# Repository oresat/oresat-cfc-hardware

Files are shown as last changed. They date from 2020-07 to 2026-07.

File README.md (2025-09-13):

# oresat-cfc-hardware

Cirrrus Flux Camera hardware repository. See also https://www.oresat.org/satellites/oresat/mission-2-cfc.

## General information
The Cirrus Flux Camera (CFC) is a Short Wave Infrared (SWIR) camera meant to map the global distribution of high-altitude cirrus clouds. It works by looking at the reflected sunlight from clouds in three SWIR bands. The primary investigators (PIs) for CFC calibration, data processing, and climate science are our collaborators at the [University of Maryland Baltimore Count (UMBC)'s Earth and Space Institute (ESI)](https://esi.umbc.edu/) as well as by our collaborators at the [University College London (UCL) Mullard Space Science Laboratory (MSSL)](https://www.ucl.ac.uk/mathematical-physical-sciences/mssl).

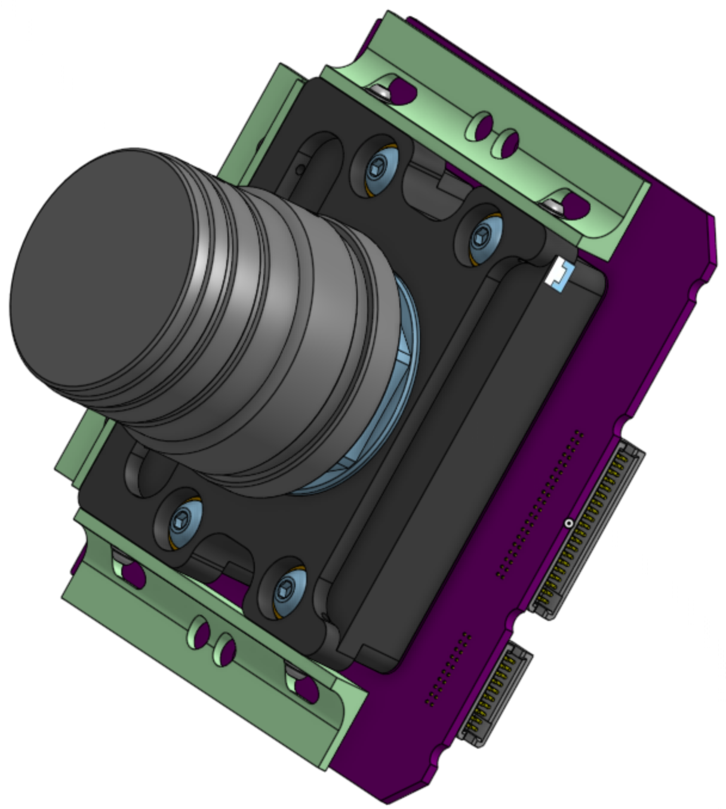
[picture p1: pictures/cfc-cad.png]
CFC Assembly CAD model


Older versions of the CFC flew on the [2022 NASA High Altitude Student Payload (HASP)](https://sg-webserver.phys.lsu.edu/) mission.

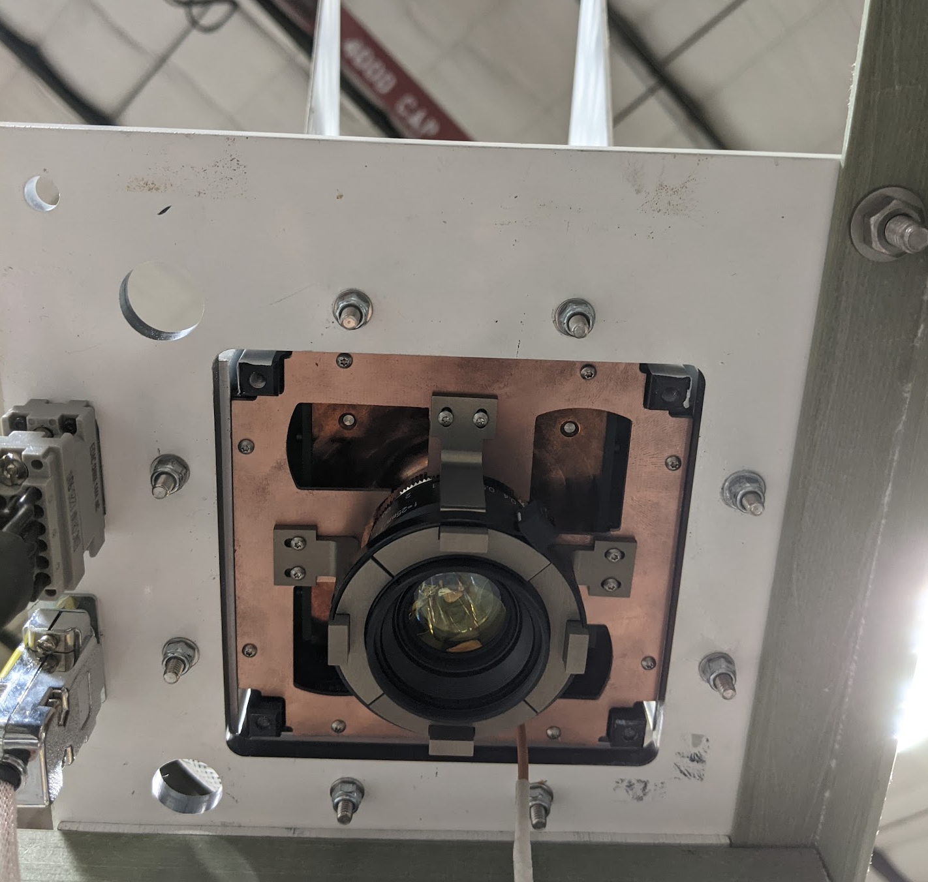
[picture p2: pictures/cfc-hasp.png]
CFC on HASP balloon


Different but modern versions were flown by [UMBC's AirHARP mission](https://esi.umbc.edu/airharp2-at-pace-pax/) on the NASA ER-2 high altitude plane.

Most recently, we flew a preliminary technology demonstration mission on [OreSat0.5](https://www.oresat.org/satellites/oresat0-5) launched August 16th, 2024.

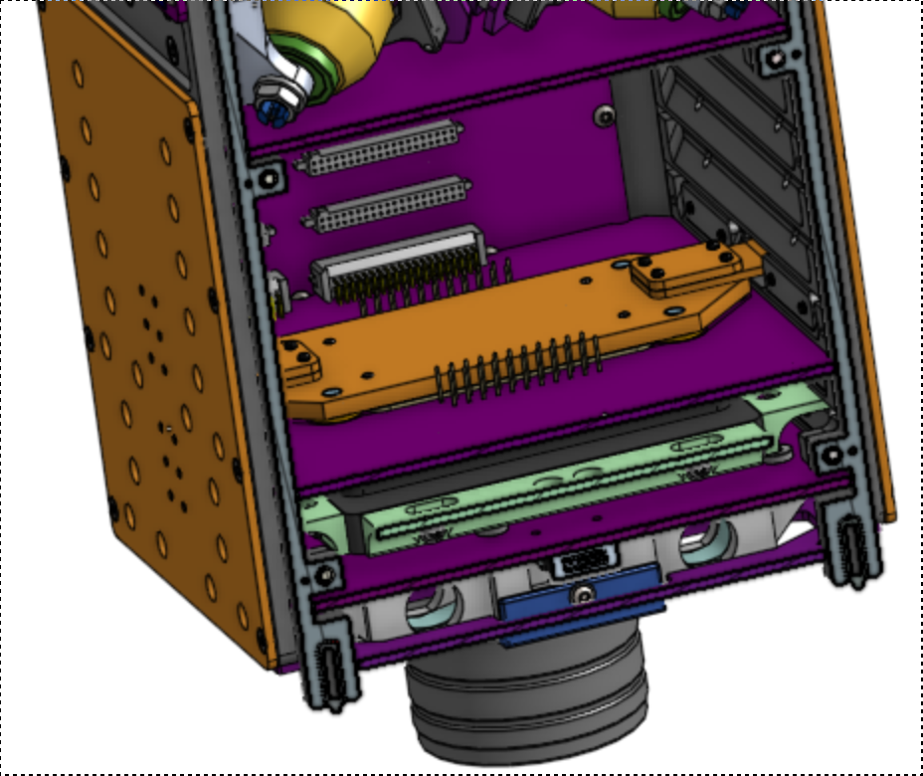
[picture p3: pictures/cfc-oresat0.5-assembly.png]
CFC on OreSat0.5


We're planning on flying the science mission camera on OreSat1 in Q2 2026.

Versions of the CFC have also flown on the NASA High Altitude Student Payload (HASP) in New Mexico, and 
## Technical information about the CFC sensor

- Princeton IR PIRT1280 InGaAs focal plane array (1280 x 1024 with 12 um pixels), sensitive to roughly 800 - 1600 nm.
- We cool the sensor to -8 deg C using its built-in thermal electric cooler (TEC - just a standard Peltier device).
- We use three filters on the PIRT1280 sensors:
   - 870 nm: [Torrent Photonics Optical Filter Shop 2020OFS-870](https://opticalfiltershop.com/shop/bandpass-filter/nir-bandpass-700nm-to-1100nm/nir-bandpass-filter-870nm-fwhm-30nm/)
   - 1390 nm: [Torrent Photonics Optical Filter Shop 2020OFS-1390](https://opticalfiltershop.com/shop/bandpass-filter/swir-bandpass-filters-1-1um-to-3-0um/swir-bandpass-filter-1390nm-fwhm-35nm/)
   - 1590 nm: [Torrent Photonics Optical Filter Shop 2020OFS-1590](https://opticalfiltershop.com/shop/bandpass-filter/swir-bandpass-filters-1-1um-to-3-0um/swir-bandpass-filter-1590nm-fwhm-40nm/)
- Lens is the [Navitar SWIR-35](https://store.navitar.com/swir-35-35-mm/), a 35 mm  SWIR lens with focus adjustable apateur. 

## Technical information on the system

- The **CFC Sensor Card** is a PCB in backplane slot 18. It has:
   - The PIRT 1280 sensor soldered on the PCB
   - A custom machined lens adapter between the card and the lens.
   - Custom machined G10 L brackets between the custom machined lens adapter and slot 19 
   - The lens on the adapter sticks through the -Z end card, through the -Z end cap, and finally out into the tuna can volume. A 3D printed adapter on the End Card holds the monopole deployers and holds the camera lens at the End Card and End Cap levels.
   - The SWIR lens sticks into the tuna-can space on the -Z end of OreSat0.5 and OreSat1.
- The **CFC Processor Card** is a PCB in backplane slot 17 with:
   - LVDS to PRU adapter IC
   - an [Octavo OSD335x-SM](https://octavosystems.com/octavo_products/osd335x-sm/) system in package (SIP) processor with 1 GB DRAM and a 16 GB eMMC storage IC.
 - Radiator
    - The top of the CFC Sensor Card has a large block of copper being used as a heat spreader. The heat spreader dumps the heat from the TEC into thin copper leaf springs that lead the heat to two external copper radiators in the -Z+Y and -Z-Y solar module positions. These copper radiators are covered by a high emissivity tape.
    
## Design Notes

- Mostly on our Google Drive right now, here's the beginnings of our [CFC Design Notes](https://docs.google.com/document/d/1nDrTuUim9k1om3DOcBtnp3ixVvrmmALAsb2CZlDwwio/edit?usp=sharing).

## Links to CAD

- [OreSat CFC Camera mechnical in OnShape](https://cad.onshape.com/documents/0e986a82427039a7549eafca/v/f54f3484c685a75ab5bd82ce/e/deddd282159689e0e52f600b)
- [OreSat0.5 containing the CFC assembly in OnShape](https://cad.onshape.com/documents/c0a6cf3367d8fdcad3a3c2e1/w/ca55e3ec6f041493d70e4b39/e/591851cdc8c634aae1522f90)
- [Electronics CAD on Github](https://github.com/oresat/oresat-cfc-hardware) - mostly KiCad with some older EAGLE files.
- [Kernel module](https://github.com/oresat/oresat-prucam-pirt1280) for the PIRT 1280 on the Octavo's PRU.

## License

All materials in this repo are copyright Portland State Aerospace Society and are licensed under the CERN Open Hardware Licence Version 2 -
Strongly Reciprocal (CERN-OHL-S v2), or any later version. A copy of the license is located in [here](LICENSE.md).

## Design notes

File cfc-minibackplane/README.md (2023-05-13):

# Oresat CFC Mini-Backplane

This is the backplane for UMBC's Air Harp 2 sensor, which is going to include a PIRT SWIR sensor using OreSat's CFC system.

## Requirements:

* Match the DXF outline from Joe, including placement of connectors and the fastener holes.
   * Probably remove solder mask from both sides of those fastener holes just in case.
   * Probably put the external connectors in the upper right hand corner.
* Use an OreSat 20 pin debug connector on this backplane so we can run USB from the CFC processor to the external connector using the CFC processor's debug connector.
* External connections
   * Power should come through a 0.2 inch euroterminal for two 20 AWG wires.
   * USB should be via a [Harwin M80-5400442](https://www.digikey.com/en/products/detail/harwin-inc/M80-5400442/4953167) connector. Pin-out is determined by us.
       * signals: USB D+, USB D-, Vbus, and GND.
       * Vbus should go through a 10k ohm resistor between the 20 pin debug connector and the Harwin connector.
       
## Required changes to the CFC Processor and CFC sensor boards

Easiest thing to do:

* Both OPDs should come on by default, so we need to bypass or hack the OPDs to turn on.
* We may want to figure out some way to power the local OPDs so they're not doing anything weird with their connections to the Octavo.

A Ben Idea:

* Add a 8.4V to 5V LDO, a Trinket M0, two 4.7K resistors, and use Oliver Rew's Arduino code to turn on both CFC cards
* This assumes we have Trinkets, which I believe we have a bunch lying around.
* This is cute because we don't have to modify the sensor or processor card, which I hate doing.
* Be careful of the 8.4V max input voltage can power the trinket without frying it (thus the 5V LDO).

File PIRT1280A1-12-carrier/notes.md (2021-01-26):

Did a large search for low noise LDOs, found the LT3042. There are various flavors; get large temperature version, automative, if possible.

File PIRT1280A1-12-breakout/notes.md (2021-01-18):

100 ohm Differential pairs on OSH Park 4 layer 
* Found the trace width here. https://www.reddit.com/r/ECE/comments/2ttd3t/differential_trace_impedance_matching_question/
* Used https://www.everythingrf.com/rf-calculators/differential-microstrip-impedance-calculator
* Used https://www.eeweb.com/tools/edge-coupled-microstrip-impedance/
* Assumptions: t = 1.4 mils, , h = 6.7 mils,  Er = 3.69
* diff microsrtips of w = 15 mils, s = 10 mils --> 100.59 differential

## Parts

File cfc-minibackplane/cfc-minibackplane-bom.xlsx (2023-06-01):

Qty | P/DNP | Parts | MFR | MPN | Description | Generic | Assembly | Stock | Dist | DPN | Notes
2 | P | C1.1, C1.2 | Murata | GCM1885C2A102JA16D | 1000 pF ±5% 100V Ceramic Capacitor C0G, NP0 0603 AEC-Q200 | Y |  |  | Digi-Key | 490-4772-1-ND | CAN termination
2 | NP | C3.1, C3.2 | Murata | GCM1885C2A102JA16D | 1000 pF ±5% 100V Ceramic Capacitor C0G, NP0 0603 AEC-Q200 | Y |  |  | Digi-Key | 490-4772-1-ND | CAN termination
4 | P | C1, C2, C3, C4 | Murata | GCM31CC71E106KA03K | 10 µF ±10% 25V Ceramic Capacitor X7S 1206 AEC-Q200 | Y |  |  | Digi-Key | 490-14533-1-ND | Note working voltage
3 | P | CF1.1, CF2.1, CF3.1 | Samtec | SFM-110-01-L-D-LC | 20 Position Receptacle Connector 0.050" (1.27mm) Through Hole Gold | N |  |  | Digi-Key | SFM-110-01-L-D-LC-ND | Auxiliary connector: Also SFM-110-[01|03|L1|L3]-[L|S|F]-D-LC
3 | P | CF1.2, CF2.2, CF3.2 | Samtec | SFM-120-01-L-D-LC | 40 Position Receptacle Connector 0.050" (1.27mm) Through Hole Gold | N |  |  | Digi-Key | SFM-120-01-L-D-LC-ND | Main connector: Also SFM-120-01-[L|S|F]-D-LC
1 | P | J1 | Harwin | M55-6001642R | 16 Position Receptacle Connector 0.050" (1.27mm) Surface Mount Gold | N |  |  | Digi-Key | 952-3836-1-ND | Backplane debug connector
1 | P | J2 | Harwin | M80-5100442 | Connector Header Through Hole 4 position 0.079" (2.00mm) | N |  |  | Digi-Key | 952-2343-ND | USB Connector
1 | P | J3 | Phoenix Contact | 1809267 | 2 Position Terminal Block Header, Male Pins, Shrouded (4 Side) 0.200" (5.08mm) Vertical Through Hole | N |  |  | Digi-Key | 277-2619-ND | Power connector
1 | P | J4 | TE | 2-1734592-0 | 20 Position FPC Connector Contacts, Bottom 0.020" (0.50mm) Surface Mount, Right Angle | N |  |  | Digi-Key | A100287CT-ND | Card debug connector
2 | P | R4, R5 | Stackpole | RMCF0603ZT0R00 | 0 Ohms Jumper Chip Resistor 0603 AEC-Q200 Thick Film | Y |  |  | Digi-Key | RMCF0603ZT0R00CT-ND | CAN jumpers
4 | P | R1.1, R1.2, R1.3, R1.4 | Rohm | ESR18EZPF60R4 | 60.4 Ohms Â±1% 0.5W, 1/2W Resistor 1206 AEC-Q200 | Y |  |  | Digi-Key | RHM60.4AFCT-ND | CAN termination
4 | NP | R3.1, R3.2, R3.3, R3.4 | Rohm | ESR18EZPF60R4 | 60.4 Ohms Â±1% 0.5W, 1/2W Resistor 1206 AEC-Q200 | Y |  |  | Digi-Key | RHM60.4AFCT-ND | CAN termination
1 | P | R2, R3 | Stackpole | RMCF0603FT4K70 | 4.7 kOhms ±1% 0.1W, 1/10W Chip Resistor 0603 (1608 Metric) Automotive AEC-Q200 Thick Film | Y |  |  | Digi-Key | RMCF0603FT4K70CT-ND | OPD pullups
1 | P | R1 | Stackpole | RMCF0603FT100K | 100 kOhms ±1% 0.1W, 1/10W Chip Resistor 0603 (1608 Metric) Automotive AEC-Q200 Thick Film | Y |  |  | Digi-Key | RMCF0603FT100KCT-ND | Vbus connection
1 | P | U1 | Adafruit Industries | 3500 | ATSAMD21E18 Trinket M0 SAM D ARM® Cortex®-M0+ MCU 32-Bit Embedded Evaluation Board | N |  |  | Digi-Key | 1528-2361-ND | OPD controller
1 | P | U2 | UMW | AMS1117-3.3 | Linear Voltage Regulator IC Positive Fixed 1 Output 1A SOT-223-3L | Y |  |  | Digi-Key | 4518-AMS1117-3.3CT-ND | 3.3V regulator
For debugging / testing
Qty | P/DNP | Parts | MFR | MPN | Description | Generic | Assembly | Stock | Dist | DPN | Notes
3 | NP | N/A | Harwin | M80-4600442 | 4 Position Rectangular Receptacle Connector Crimp Gold 22 AWG | N |  |  | Digi-Key | 952-2625-ND | USB connector
3 | NP | N/A | Phoenix Contact | 1757019 | 2 Position Terminal Block Plug, Female Sockets 0.200" (5.08mm) 180° Free Hanging (In-Line) | N |  |  | Digi-Key | 277-1011-ND | Power connector. Alternative: 1861690

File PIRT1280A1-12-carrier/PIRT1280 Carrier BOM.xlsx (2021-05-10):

Qty | Parts | MFR | MPN | Description | DIS | DPN
6 | C19, C22, C28, C29, C32, C37 | Murata | GCM155R71H102KA37D | CAP CER 1000PF 50V X7R 0402 | Digi-Key | 490-4761-1-ND
6 | C20, C23, C27, C30, C33, C36 | Murata | GCM155R71H103KA55D | CAP CER 10000PF 50V X7R 0402 | Digi-Key | 490-4762-1-ND
5 | C12, C13, C14, C15, C16 | TDK | CGA3E3X5R1E474K080AB | CAP CER 0.47UF 25V X5R 0603 | Digi-Key | 445-12468-1-ND
6 | C21, C24, C26, C31, C34, C35 | Murata | GCM155R71H104KE02J | CAP CER 0.1UF 50V X7R 0402 | Digi-Key | 490-14514-1-ND
3 | C11, C18, C40 | TDK | CGA3E2X8R1E104K080AA | CAP CER 0.1UF 25V X8R 0603 | Digi-Key | 445-5885-1-ND
1 | C17 | TDK | CGA3E1X7R1E105K080AC | CAP CER 1UF 25V X7R 0603 | Digi-Key | 445-6931-1-ND
10 | C1, C2, C3, C4, C5, C6, C7, C8, C9, C10 | TDK | CGA3E1X5R0J475K080AC | CAP CER 4.7UF 6.3V X5R 0603 | Digi-Key | 445-6934-1-ND
1 | C25 | Murata | GRT188R61C106KE13J | CAP CER 10UF 16V X5R 0603 | Digi-Key | 490-GRT188R61C106KE13JTR-ND
2 | D1, D2 | Vishay | TLMG1100-GS08 | LED GREEN 0603 SMD | Digi-Key | 751-1165-1-ND
1 | FB1 | Murata | BLM18KG300JH1D | FERRITE BEAD 30 OHM 0603 1 LN | Digi-Key | 490-14027-1-ND
1 | J12 | TE | 292303-7 | USB-A (USB TYPE-A) USB 2.0 Receptacle Connector 4 Position SMT,RA ; TH | Digi-Key | A115151-ND
1 | J13 | Molex | 395430002 | 2 Position Wire to Board Terminal Block Horizontal 5.00mm TH | Digi-Key | WM12755-ND
1 | J14 | CUI | PJ-202A | Power Barrel Connector Jack 2.10mm ID 5.50mm OD TH RA | Digi-Key | CP-202A-ND
1 | J9 | Wurth | 68715014522 | 50 Position FPC Connector Contacts, Bottom 0.020" (0.50mm) SMT RA | Digi-Key | 732-3522-1-ND
1 | PCB1 | GHI | POCKETBEAGLE-SC-569 | OSD3358 PocketBeagle series ARM® Cortex®-A8 MPU Embedded Evaluation Board | Digi-Key | POCKETBEAGLE-SC-569-ND
1 | Q1 | On Semi | FDD8782 | N-Channel 35A (Tc) 50W (Tc) Surface Mount TO-252AA | Digi-Key | FDD8782TR-ND
5 | R13, R14, R15, R16, R17 | Vishay | MCT0603MZ0000ZP500 | 0 RESISTOR .0603-A | Digi-Key | 749-1745-1-ND
3 | R25, R26, R27 | Stackpole | RMCF0402FT100R | 100 ±1% 0.063W, 1/16W Chip Resistor 0402 AEC-Q200 Thick Film | Digi-Key | RMCF0402FT100RCT-ND
2 | R1, R28 | Panasonic | ERJ-3EKF1001V | 1k RESISTOR .0603-A | Digi-Key | P1.00KHCT-ND
1 | R4 | Panasonic | ERJ-3EKF9091V | 9.09k RESISTOR .0603-A | Digi-Key | P9.09KHCT-ND
1 | R2 | Panasonic | EXB-2HV103JV | 10k RES_EXB2HV | Digi-Key | Y1103CT-ND
1 | R20 | Panasonic | EXB-A10P103J | 10k ARRAY_EXBA-M | Digi-Key | U7103CT-ND
1 | R5 | Panasonic | ERJ-3EKF1622V | 16.2k RESISTOR .0603-A | Digi-Key | P16.2KHCT-ND
1 | R19 | Panasonic | ERJ-6ENF2052V | 20k RESISTOR .0805-A | Digi-Key | P20.5KCCT-ND
1 | R3 | Panasonic | ERJ-3EKF2942V | 29.4k RESISTOR .0603-A | Digi-Key | P29.4KHCT-ND
2 | R6, R7 | Panasonic | ERJ-3EKF33R2V | 33.2k RESISTOR .0603-A | Digi-Key | P33.2HCT-ND
1 | R18 | Panasonic | ERJ-6ENF2053V | 200k RESISTOR .0805-A | Digi-Key | P205KCCT-ND
5 | U1, U2, U3, U4, U5 | Analog Devices | LT3042IMSE#TRPBF | Linear Voltage Regulator IC Positive Adjustable Output 200mA 10-MSOP-EP | Digi-Key | LT3042IMSE#TRPBFCT-ND
1 | U6 | TI | LM2901QPWRQ1 | Comparator Differential CMOS, MOS, Open-Collector, TTL 14-TSSOP | Digi-Key | 296-18438-1-ND
1 | U7 | TI | DS90CR218AMTD/NOPB | 3.3V Rising Edge Data Strobe LVDS 21-Bit Channel Link - 12 Mhz to 85 Mhz | Digi-Key | DS90CR218AMTD/NOPB-ND
1 | X1 | Abracon | ASDAIG-16.000MHZ-X-K-S-T | OSC XO 16.000MHZ 3.3V CMOS SMD | Digi-Key | 535-ASDAIG-16.000MHZ-X-K-S-TCT-ND
ON BREAKOUT BOARD
1 | J1 | Wurth | 68715014522 | 50 Position FPC Connector Contacts, Bottom 0.020" (0.50mm) SMT RA | Digi-Key | 732-3522-1-ND
5 | C100, C101, C102, C103, C104 | AVX | 08055C104K4T4A | 100n ±10% 50V Ceramic Capacitor X7R 0805 | Digi-Key | 478-10546-1-ND

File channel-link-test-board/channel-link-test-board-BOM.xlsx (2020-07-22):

Bill Of Materials for Channel Link Test Board
source file: channel-link-test-board.sch
Last modified: 2020/07/21
PCB version: 1.0 |  |  | P/DNP = | Place/Do Not Place (DNP is for final production boards)
BOM revision: 1 |  |  | Generic = | Any generic part with the same characteristics are OK (e.g., bypass cap)
Cnt | Part References | P/DNP | Mfg | Mfg PN | Description | Generic | Dist | Dist Part Number
1 | JP3 | P | Wurth | 61300311121 | CONN HEADER VERT 3POS 2.54MM | Y | Digi-Key | 732-5316-ND
2 | JP1, JP2 | P | Amphenol | 71918-160LF | CONN HEADER VERT 60POS 2.54MM | Y | Digi-Key | 609-3528-ND
4 | R1, R2, R3, R4 | P | Yageo | RC0201FR-07100RL | RES SMD 100 OHM 1% 1/20W 0201 | Y | Dgi-Key | 311-100MCT-ND
2 | R5, R6 | P | Yageo | RC0603FR-07100RL | RES SMD 100 OHM 1% 1/10W 0603 | Y | Digi-Key | 311-100HRCT-ND
12 | C13, C15, C16, C17, C18, C32, C33, C34, C35, C36, C14, C31 | P | Kemet | C0805C104Z5VACTU | CAP CER 0.1UF 50V Y5V 0805 | Y | Digi-Key | 399-1177-1-ND
1 | R7 | P | Yageo | RC0603FR-0710KL | RES SMD 10K OHM 1% 1/10W 0603 | Y | Digi-Key | 311-10.0KHRCT-ND
12 | C7, C8, C9, C10, C11, C26, C27, C28, C29, C30, C12, C25 | P | Kemet | C0603C103M5RACTU | CAP CER 10000PF 50V X7R 0603 | Y | Digi-Key | 399-7842-1-ND
2 | C37, C38 | P | Murata | GRM188R61A106KE69J | CAP CER 10UF 10V X5R 0603 | Y | Digi-Key | 490-14372-1-ND
12 | C1, C2, C3, C4, C5, C6, C19, C20, C21, C22, C23, C24 | P | Murata | GRM155R71H102KA01J | CAP CER 1000PF 50V X7R 0402 | Y | Digi-Key | 490-6350-1-ND
1 | U1 | P | Texas Instruments | DS90CR218AMTD/NOPB | IC INTERFACE SPECIALIZED 48TSSOP | N | Digi-Key | DS90CR218AMTD/NOPB-ND
1 | U2 | P | Texas Instruments | DS90CR218AMTD/NOPB | IC INTERFACE SPECIALIZED 48TSSOP | N | Digi-Key | DS90CR218AMTD/NOPB-ND

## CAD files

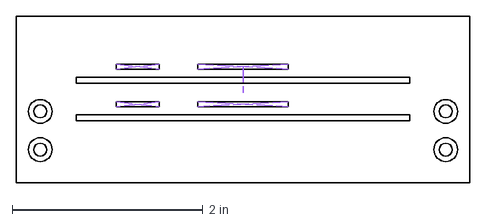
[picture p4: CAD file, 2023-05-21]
cfc-minibackplane/AH2_SWIRminiBackplaneBoard_2023-05-18.dxf
4.75 x 1.75 in

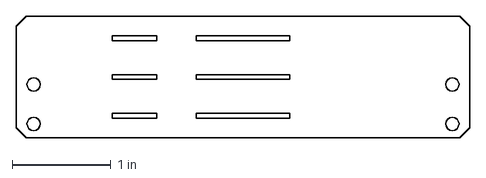
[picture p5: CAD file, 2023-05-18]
cfc-minibackplane/AH2_SWIRminiBackplaneBoard_2023-05-16.dxf
4.60 x 1.23 in

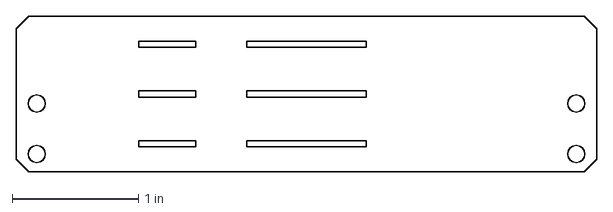
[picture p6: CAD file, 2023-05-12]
cfc-minibackplane/cfc-minibackplane.dxf
4.60 x 1.23 in

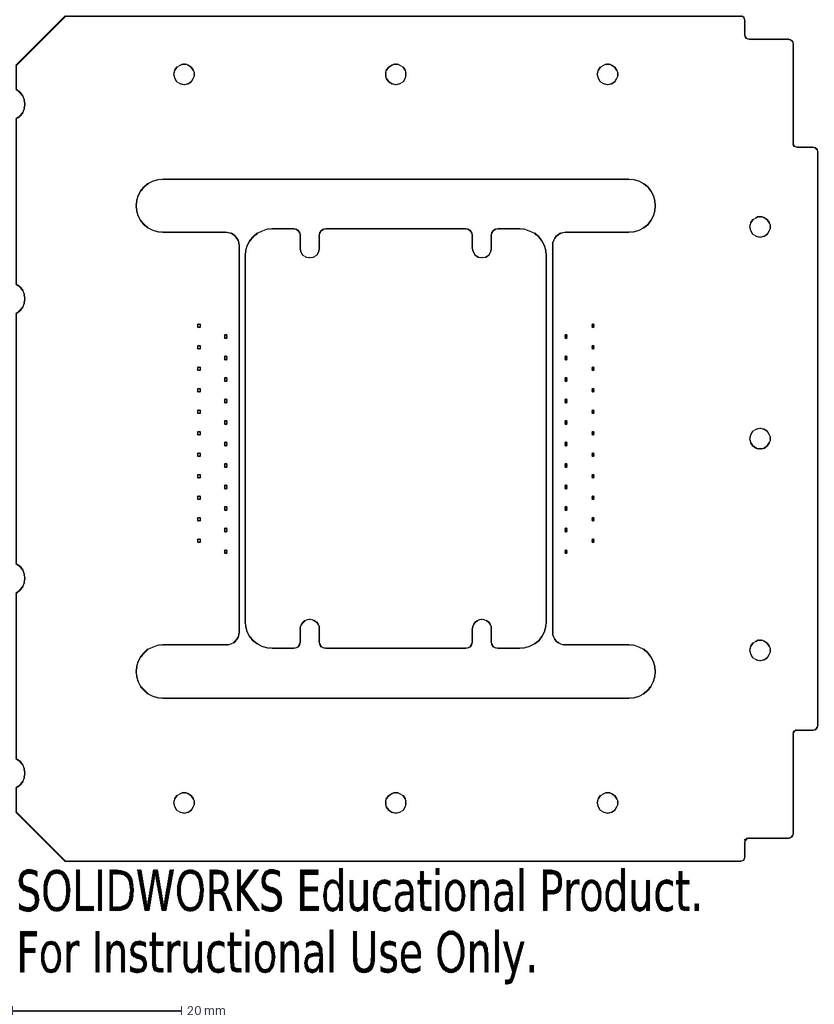
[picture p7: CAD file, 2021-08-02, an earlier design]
cfc-sensor-card-v1/CFCcard.DXF
SOLIDWORKS Educational Product.
For Instructional Use Only.

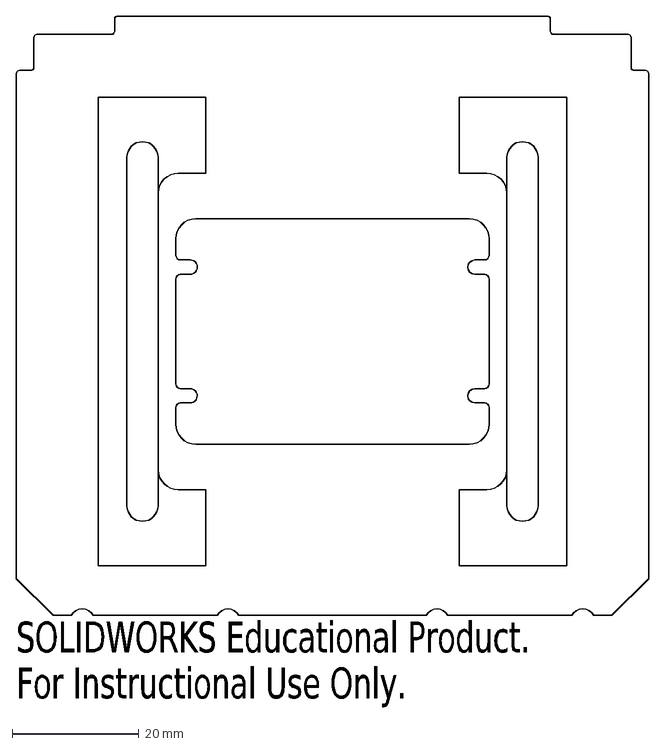
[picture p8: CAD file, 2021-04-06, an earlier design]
cfc-sensor-card-v1/CFCdxf.DXF
SOLIDWORKS Educational Product.
For Instructional Use Only.

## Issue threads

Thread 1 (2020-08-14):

CFC Processor: PLL_VCC and PLL_GND are swapped on the DS90CR217

davidalay, 2020-08-14:
The PLL_VCC and PLL_GND pins need to be swapped on the DS90CR217, currently the board will short with a 30 ohm impedance without a mod.  The footprint on the DS90CR218 is correct

andrewgreenberg, 2025-09-14:
This was fixed as far as I can tell long ago.

Closed 2025-09-14.

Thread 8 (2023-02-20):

Sensor Card v2: Q6 gate missing 10k pulldown

NickLekas, 2023-02-20:

andrewgreenberg, 2025-09-13:
Done!

Closed 2025-09-13.

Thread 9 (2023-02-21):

Sensor Card V2: C23 and R56 should be swapped

oliver-rew, 2023-02-21:
C23 should be closer to the LDO and R56 should be further, to match the layout of the other LDOs.

andrewgreenberg, 2025-09-13:
Done!

Closed 2025-09-13.

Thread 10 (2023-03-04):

CFC Processor: PRU0_14 and PRU0_15 connected to wrong octavo pins

oliver-rew, 2023-03-04:
I just noticed that the PRU0_14 and PRU0_15 lines on the camera bus are connected to the completely incorrect pins! They are currently connected to GPMC_AD12 and GPMC_AD13, respectively, when they should be GPMC_AD14 and GPMC_AD15. GPMC_AD14 and GPMC_AD15 are the pins the connected to 'pr1_pru0_pru_r31_14' and 'pr1_pru0_pru_r31_15' internally, which are the PRU inputs we need. See the star-tracker card for reference, where they are connected to the correct pins. This would be a massive, unfixable bug except that those pins aren't used on the CFC card, I guess I just copied them over incorrectly even though they aren't used.

WRONG:
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

RIGHT:
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

Since these aren't connected to anything, we should just remove them.

andrewgreenberg, 2025-09-14:
These pins are removed in the v2.0 board.

Closed 2025-09-14.

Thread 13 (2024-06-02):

Power status pin between cards

ryanpdx, 2024-06-02:
It would be great to have a power status pin between the cfc processor and cfc sensor cards, so the cfc processor know the cfc sensor is on, off, or missing.

andrewgreenberg, 2025-09-13:
This would be great, but there's no room on the AUX connector and it would be crazy to put this on the main connctor. I've put a note about this on the schematic, where it'll live forever since I don't think we're ever redoing this board.

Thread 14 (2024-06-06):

Sensor Card: Add holes for heat spreader locator pins

andrewgreenberg, 2024-06-06:
UMBC complained that the heat spreader can be misaligned by quite a bit. Those M4 fasteners and the PIRT sensor pins don't do a good job locating it, it's true. So let's add two locating holes in the PCB, and add pins (like the 1.5 mm pins we use for the RWs) to the copper heat spreader.

andrewgreenberg, 2025-09-13:
Added 1.5 mm holes in v2.1 of sensor card, centered between fastener hole passthroughts

Closed 2025-09-13.

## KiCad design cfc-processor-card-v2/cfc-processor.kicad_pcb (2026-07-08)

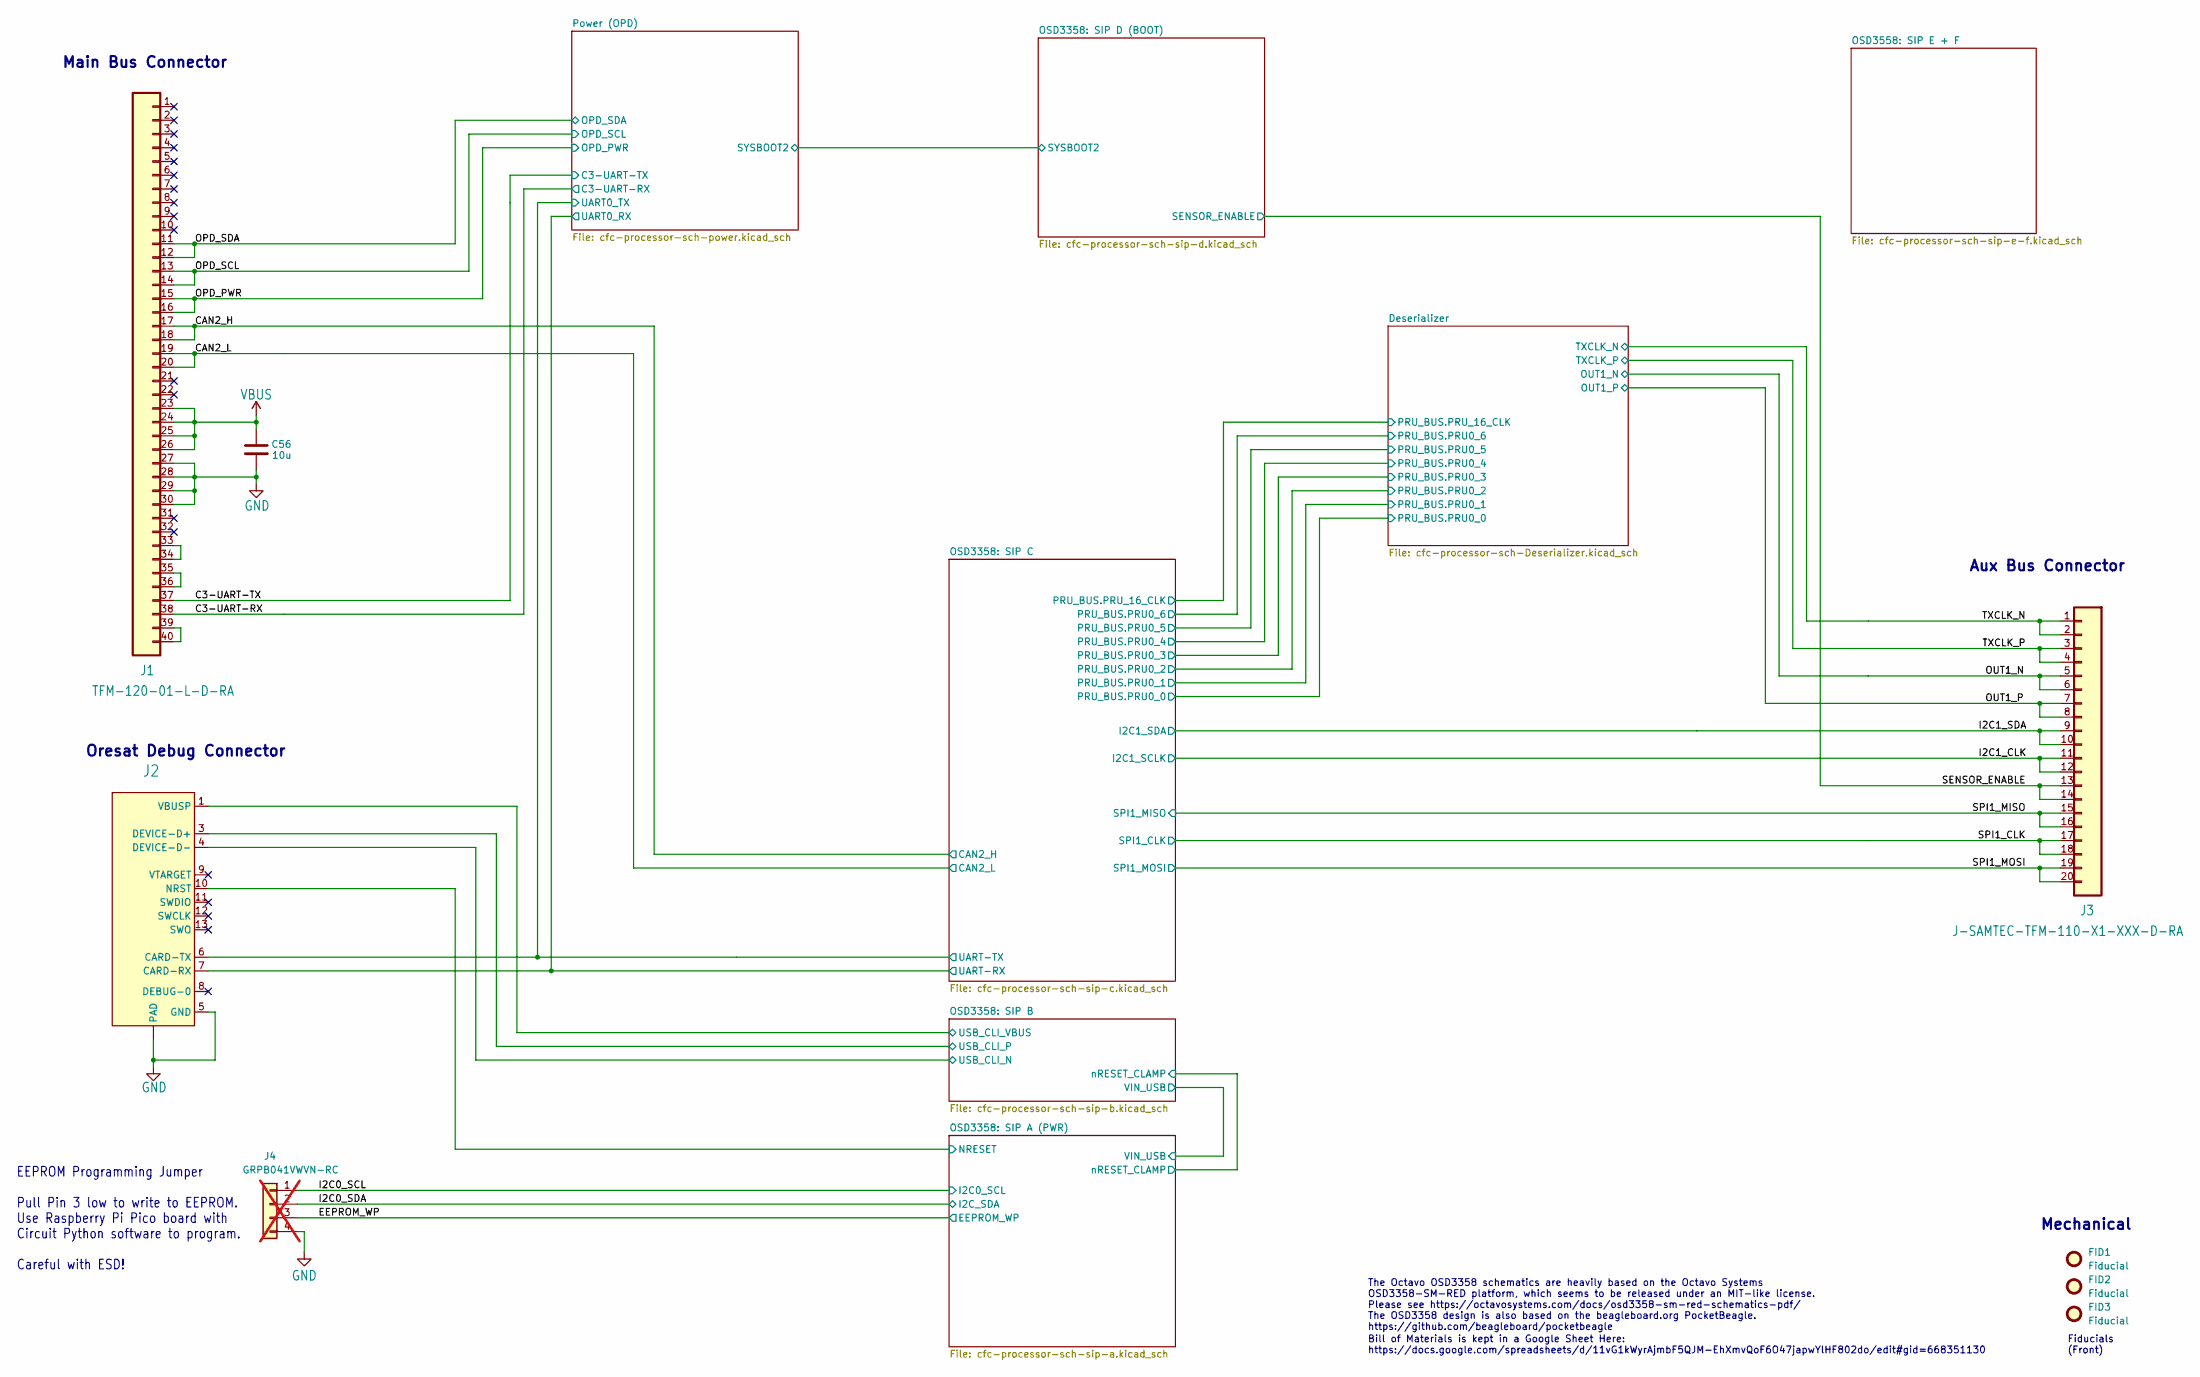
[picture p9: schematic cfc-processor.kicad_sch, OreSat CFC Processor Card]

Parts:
C56: 10u; 0805-B-NOSILK; MPN CL21B106KAYQNNE
FID1, FID2, FID3: Fiducial; Fiducial_1mm_Mask2mm
J1: TFM-120-01-L-D-RA; J-SAMTEC-TFM-120-X1-XXX-D-RA; MPN TFM-120-01-L-D-RA
J2: 2-1734592-0; J-JST-SM14BSHLSTF; MPN SM14B-SHLS-TF
J3: J-SAMTEC-TFM-110-X1-XXX-D-RA; MPN TFM-110-01-L-D-RA
J4: GRPB041VWVN-RC; PinHeader_1x04_P1.27mm_Vertical; MPN GRPB041VWVN-RC; not fitted

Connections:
/C3-UART-RX: J1.38; also elsewhere on the board
/C3-UART-TX: J1.37; also elsewhere on the board
/CAN2_H: J1.17, J1.18; also elsewhere on the board
/CAN2_L: J1.19, J1.20; also elsewhere on the board
/EEPROM_WP: J4.3; also elsewhere on the board
/I2C0_SCL: J4.1; also elsewhere on the board
/I2C0_SDA: J4.2; also elsewhere on the board
/I2C1_CLK: J3.11, J3.12; also elsewhere on the board
/I2C1_SDA: J3.9, J3.10; also elsewhere on the board
/OPD_PWR: J1.15, J1.16; also elsewhere on the board
/OPD_SCL: J1.13, J1.14; also elsewhere on the board
/OPD_SDA: J1.11, J1.12; also elsewhere on the board
/OSD3358: SIP A (PWR)/NRESET: J2.10 (NRST); also elsewhere on the board
/OSD3358: SIP B/USB_CLI_N: J2.4 (DEVICE-D-); also elsewhere on the board
/OSD3358: SIP B/USB_CLI_P: J2.3 (DEVICE-D+); also elsewhere on the board
/OSD3358: SIP B/USB_CLI_VBUS: J2.1 (VBUSP), J2.2 (VBUSP); also elsewhere on the board
/OSD3358: SIP C/UART-RX: J2.7 (CARD-RX); also elsewhere on the board
/OSD3358: SIP C/UART-TX: J2.6 (CARD-TX); also elsewhere on the board
/OUT1_N: J3.5, J3.6; also elsewhere on the board
/OUT1_P: J3.7, J3.8; also elsewhere on the board
/SENSOR_ENABLE: J3.13, J3.14; also elsewhere on the board
/SPI1_CLK: J3.17, J3.18; also elsewhere on the board
/SPI1_MISO: J3.15, J3.16; also elsewhere on the board
/SPI1_MOSI: J3.19, J3.20; also elsewhere on the board
/TXCLK_N: J3.1, J3.2; also elsewhere on the board
/TXCLK_P: J3.3, J3.4; also elsewhere on the board
GND: C56.2, J1.27, J1.28, J1.29, J1.30, J2.5 (GND), J2.14 (GND), J2.15 (PAD), J2.16 (PAD), J4.4; also elsewhere on the board
unnamed: J1.33, J1.34
unnamed: J1.35, J1.36
unnamed: J1.39, J1.40
VBUS: C56.1, J1.23, J1.24, J1.25, J1.26; also elsewhere on the board

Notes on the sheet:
Bill of Materials is kept in a Google Sheet Here: https://docs.google.com/spreadsheets/d/11vG1kWyrAjmbF5QJM-EhXmvQoF6O47japwYlHF802do/edit#gid=668351130
EEPROM Programming Jumper Pull Pin 3 low to write to EEPROM. Use Raspberry Pi Pico board with Circuit Python software to program. Careful with ESD!
The OSD3358 design is also based on the beagleboard.org PocketBeagle. https://github.com/beagleboard/pocketbeagle
Mechanical
Fiducials (Front)
Main Bus Connector
The Octavo OSD3358 schematics are heavily based on the Octavo Systems OSD3358-SM-RED platform, which seems to be released under an MIT-like license. Please see https://octavosystems.com/docs/osd3358-sm-red-schematics-pdf/
Aux Bus Connector
Oresat Debug Connector

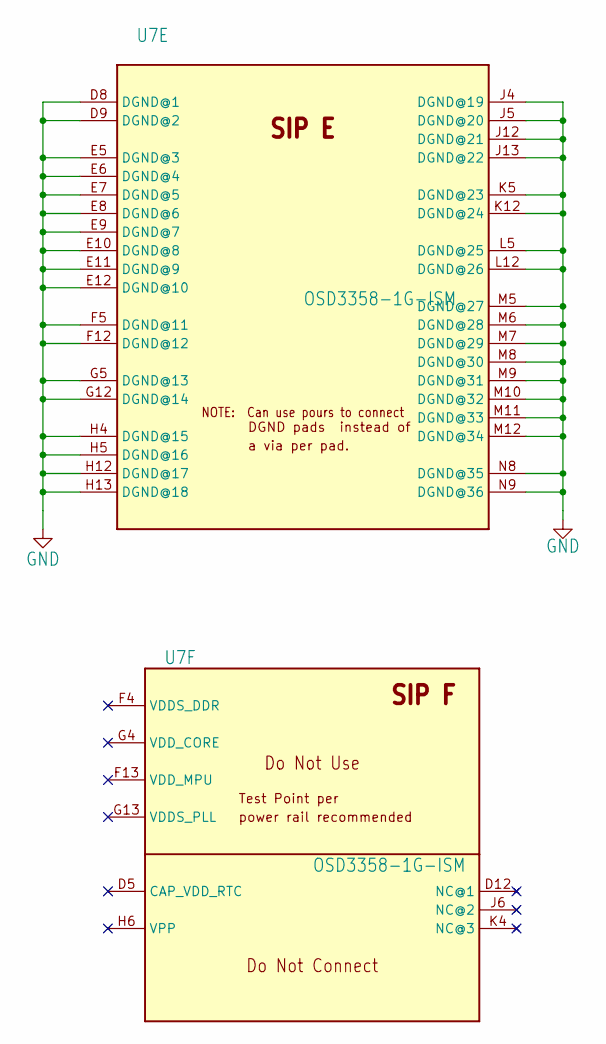
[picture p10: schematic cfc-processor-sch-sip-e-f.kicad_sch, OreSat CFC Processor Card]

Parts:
U7: OSD3358-1G-ISM; U-Octavo-OSD335X-BGA-256; MPN OSD3358-1G-ISM

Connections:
GND: U7.D8 (DGND@1), U7.D9 (DGND@2), U7.E5 (DGND@3), U7.E6 (DGND@4), U7.E7 (DGND@5), U7.E8 (DGND@6), U7.E9 (DGND@7), U7.E10 (DGND@8), U7.E11 (DGND@9), U7.E12 (DGND@10), U7.F5 (DGND@11), U7.F12 (DGND@12), U7.G5 (DGND@13), U7.G12 (DGND@14), U7.H4 (DGND@15), U7.H5 (DGND@16), U7.H12 (DGND@17), U7.H13 (DGND@18), U7.J4 (DGND@19), U7.J5 (DGND@20), U7.J12 (DGND@21), U7.J13 (DGND@22), U7.K5 (DGND@23), U7.K12 (DGND@24), U7.L5 (DGND@25), U7.L12 (DGND@26), U7.M5 (DGND@27), U7.M6 (DGND@28), U7.M7 (DGND@29), U7.M8 (DGND@30), U7.M9 (DGND@31), U7.M10 (DGND@32), U7.M11 (DGND@33), U7.M12 (DGND@34), U7.N8 (DGND@35), U7.N9 (DGND@36); also elsewhere on the board

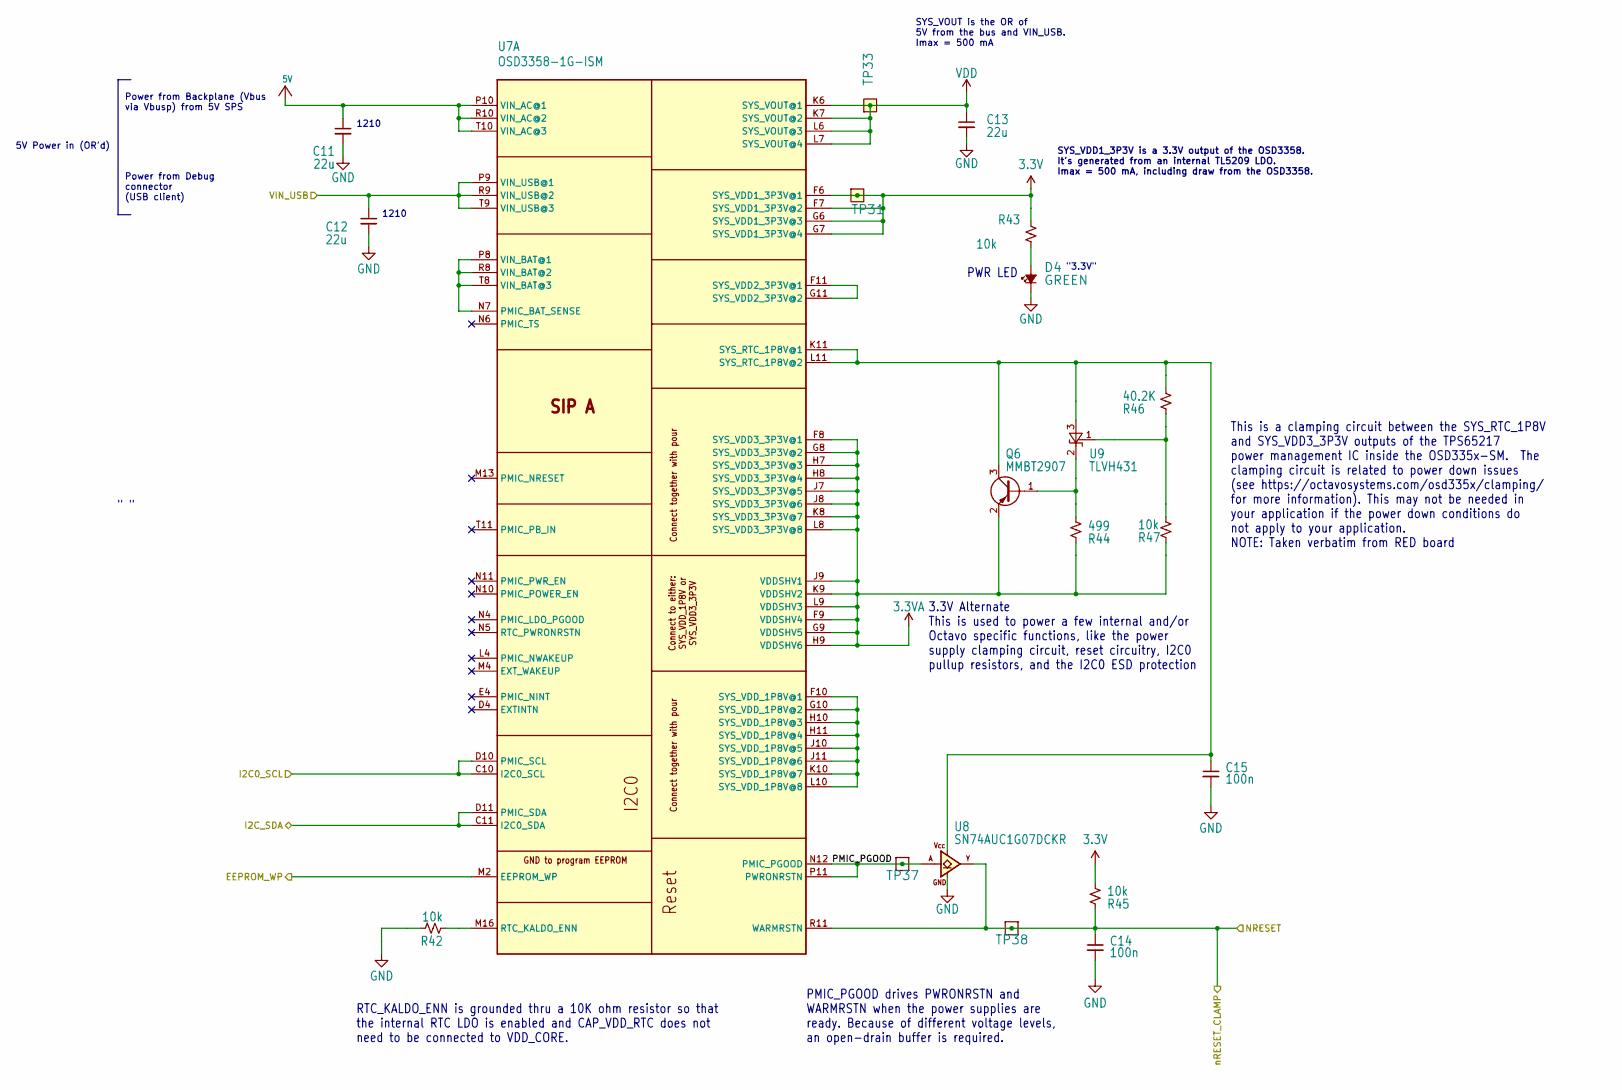
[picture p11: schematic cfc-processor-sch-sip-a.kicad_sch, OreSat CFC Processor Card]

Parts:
C11, C12, C13: 22u; C_1210_3225Metric; MPN TMK325B7226KMHP
C14, C15: 100n; 0603-C-NOSILK; MPN C0603C104K5RACAUTO
D4: GREEN; LED_0603_1608Metric; MPN 150060GS75000
Q6: MMBT2907; SOT-23; MPN PMBT2907A,235
R42, R43, R45, R47: 10k; 0603-C-NOSILK; MPN RMCF0603FT10K0
R44: 499; 0603-C-NOSILK; MPN RMCF0603FT499R
R46: 40.2K; 0603-C-NOSILK; MPN RMCF0603FT40K2
TP31: TEST-POINT; TestPoint-0.75mm-th
TP33: TEST-POINT3X4; TestPoint-0.75mm-th
TP37, TP38: TEST-POINT3X4; TestPoint_Pad_D1.0mm
U7: OSD3358-1G-ISM; U-Octavo-OSD335X-BGA-256; MPN OSD3358-1G-ISM
U8: SN74AUC1G07DCKR; SOT-353_SC-70-5; MPN SN74AUC1G07DCKR
U9: TLVH431; SOT-23; MPN TLVH431BCDBZT

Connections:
3.3V: R43.1, R45.1, TP31.1 (1_1), U7.F6 (SYS_VDD1_3P3V@1), U7.F7 (SYS_VDD1_3P3V@2), U7.G6 (SYS_VDD1_3P3V@3), U7.G7 (SYS_VDD1_3P3V@4); also elsewhere on the board
3.3VA: Q6.2 (E), R44.2, R47.2, U7.F8 (SYS_VDD3_3P3V@1), U7.F9 (VDDSHV4), U7.G8 (SYS_VDD3_3P3V@2), U7.G9 (VDDSHV5), U7.H7 (SYS_VDD3_3P3V@3), U7.H8 (SYS_VDD3_3P3V@4), U7.H9 (VDDSHV6), U7.J7 (SYS_VDD3_3P3V@5), U7.J8 (SYS_VDD3_3P3V@6), U7.J9 (VDDSHV1), U7.K8 (SYS_VDD3_3P3V@7), U7.K9 (VDDSHV2), U7.L8 (SYS_VDD3_3P3V@8), U7.L9 (VDDSHV3)
5V: C11.1, U7.P10 (VIN_AC@1), U7.R10 (VIN_AC@2), U7.T10 (VIN_AC@3); also elsewhere on the board
/EEPROM_WP: U7.M2 (EEPROM_WP); also elsewhere on the board
/I2C0_SCL: U7.C10 (I2C0_SCL), U7.D10 (PMIC_SCL); also elsewhere on the board
/I2C0_SDA: U7.C11 (I2C0_SDA), U7.D11 (PMIC_SDA); also elsewhere on the board
/OSD3358: SIP A (PWR)/NRESET: C14.1, R45.2, TP38.1 (1_1), U7.R11 (WARMRSTN), U8.4 (Y); also elsewhere on the board
/OSD3358: SIP A (PWR)/PMIC_PGOOD: TP37.1 (1_1), U7.N12 (PMIC_PGOOD), U7.P11 (PWRONRSTN), U8.2 (A)
/OSD3358: SIP A (PWR)/VIN_USB: C12.1, U7.P9 (VIN_USB@1), U7.R9 (VIN_USB@2), U7.T9 (VIN_USB@3); also elsewhere on the board
GND: C11.2, C12.2, C13.2, C14.2, C15.2, D4.1 (K), R42.1, U8.3 (GND); also elsewhere on the board
unnamed: D4.2 (A), R43.2
unnamed: Q6.1 (B), R44.1, U9.2 (K)
unnamed: C15.1, Q6.3 (C), R46.1, U7.K11 (SYS_RTC_1P8V@1), U7.L11 (SYS_RTC_1P8V@2), U8.5 (VCC), U9.3 (A)
unnamed: U7.N7 (PMIC_BAT_SENSE), U7.P8 (VIN_BAT@1), U7.R8 (VIN_BAT@2), U7.T8 (VIN_BAT@3)
unnamed: R42.2, U7.M16 (RTC_KALDO_ENN)
unnamed: U7.F11 (SYS_VDD2_3P3V@1), U7.G11 (SYS_VDD2_3P3V@2)
unnamed: U7.F10 (SYS_VDD_1P8V@1), U7.G10 (SYS_VDD_1P8V@2), U7.H10 (SYS_VDD_1P8V@3), U7.H11 (SYS_VDD_1P8V@4), U7.J10 (SYS_VDD_1P8V@5), U7.J11 (SYS_VDD_1P8V@6), U7.K10 (SYS_VDD_1P8V@7), U7.L10 (SYS_VDD_1P8V@8)
unnamed: R46.2, R47.1, U9.1 (REF)
VDD: C13.1, TP33.1 (1_1), U7.K6 (SYS_VOUT@1), U7.K7 (SYS_VOUT@2), U7.L6 (SYS_VOUT@3), U7.L7 (SYS_VOUT@4)

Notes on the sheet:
SYS_VDD1_3P3V is a 3.3V output of the OSD3358. It's generated from an internal TL5209 LDO. Imax = 500 mA, including draw from the OSD3358.
PMIC_PGOOD drives PWRONRSTN and WARMRSTN when the power supplies are ready. Because of different voltage levels, an open-drain buffer is required.
" "
5V Power in (OR'd)
RTC_KALDO_ENN is grounded thru a 10K ohm resistor so that the internal RTC LDO is enabled and CAP_VDD_RTC does not need to be connected to VDD_CORE.
This is a clamping circuit between the SYS_RTC_1P8V and SYS_VDD3_3P3V outputs of the TPS65217 power management IC inside the OSD335x-SM. The clamping circuit is related to power down issues (see https://octavosystems.com/osd335x/clamping/ for more information). This may not be needed in your applic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
"3.3V"
PWR LED
1210
SYS_VOUT is the OR of 5V from the bus and VIN_USB. Imax = 500 mA
Power from Debug connector (USB client)
3.3V Alternate This is used to power a few internal and/or Octavo specific functions, like the power supply clamping circuit, reset circuitry, I2C0 pullup resistors, and the I2C0 ESD protection
Power from Backplane (Vbus via Vbusp) from 5V SPS

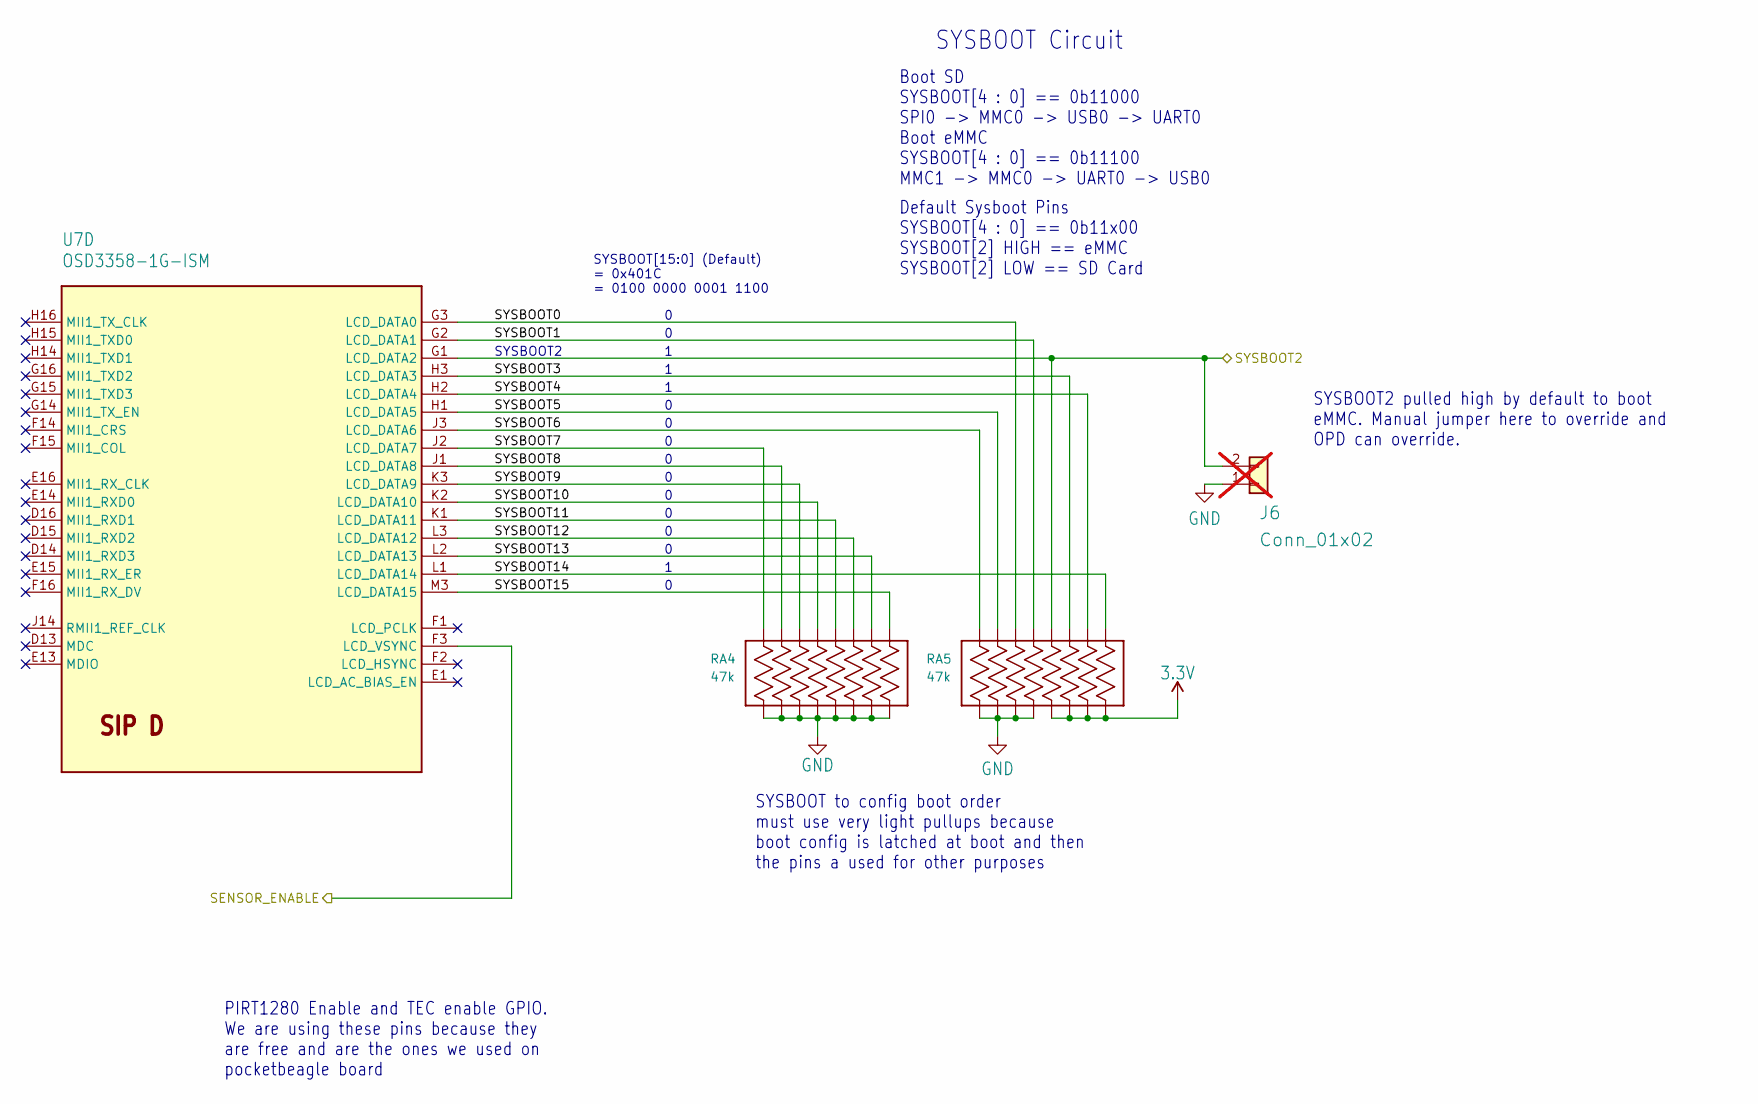
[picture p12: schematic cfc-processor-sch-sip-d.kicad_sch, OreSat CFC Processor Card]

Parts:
J6: Conn_01x02; PinHeader_1x02_P2.54mm_Vertical; not fitted
RA4, RA5: 47k; RES_EXB2HV; MPN EXB-2HV473JV
U7: OSD3358-1G-ISM; U-Octavo-OSD335X-BGA-256; MPN OSD3358-1G-ISM

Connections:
3.3V: RA5.5, RA5.6, RA5.7, RA5.8; also elsewhere on the board
/OSD3358: SIP D (BOOT)/SYSBOOT0: RA5.14, U7.G3 (LCD_DATA0)
/OSD3358: SIP D (BOOT)/SYSBOOT1: RA5.13, U7.G2 (LCD_DATA1)
/OSD3358: SIP D (BOOT)/SYSBOOT2: J6.2, RA5.12, U7.G1 (LCD_DATA2); also elsewhere on the board
/OSD3358: SIP D (BOOT)/SYSBOOT3: RA5.11, U7.H3 (LCD_DATA3)
/OSD3358: SIP D (BOOT)/SYSBOOT4: RA5.10, U7.H2 (LCD_DATA4)
/OSD3358: SIP D (BOOT)/SYSBOOT5: RA5.15, U7.H1 (LCD_DATA5)
/OSD3358: SIP D (BOOT)/SYSBOOT6: RA5.16, U7.J3 (LCD_DATA6)
/OSD3358: SIP D (BOOT)/SYSBOOT7: RA4.16, U7.J2 (LCD_DATA7)
/OSD3358: SIP D (BOOT)/SYSBOOT8: RA4.15, U7.J1 (LCD_DATA8)
/OSD3358: SIP D (BOOT)/SYSBOOT9: RA4.14, U7.K3 (LCD_DATA9)
/OSD3358: SIP D (BOOT)/SYSBOOT10: RA4.13, U7.K2 (LCD_DATA10)
/OSD3358: SIP D (BOOT)/SYSBOOT11: RA4.12, U7.K1 (LCD_DATA11)
/OSD3358: SIP D (BOOT)/SYSBOOT12: RA4.11, U7.L3 (LCD_DATA12)
/OSD3358: SIP D (BOOT)/SYSBOOT13: RA4.10, U7.L2 (LCD_DATA13)
/OSD3358: SIP D (BOOT)/SYSBOOT14: RA5.9, U7.L1 (LCD_DATA14)
/OSD3358: SIP D (BOOT)/SYSBOOT15: RA4.9, U7.M3 (LCD_DATA15)
/SENSOR_ENABLE: U7.F3 (LCD_VSYNC); also elsewhere on the board
GND: J6.1, RA4.1, RA4.2, RA4.3, RA4.4, RA4.5, RA4.6, RA4.7, RA4.8, RA5.1, RA5.2, RA5.3, RA5.4; also elsewhere on the board

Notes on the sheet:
PIRT1280 Enable and TEC enable GPIO. We are using these pins because they are free and are the ones we used on pocketbeagle board
SYSBOOT Circuit
SYSBOOT[15:0] (Default) = 0x401C = 0100 0000 0001 1100
Boot SD SYSBOOT[4 : 0] == 0b11000 SPI0 -> MMC0 -> USB0 -> UART0 Boot eMMC SYSBOOT[4 : 0] == 0b11100 MMC1 -> MMC0 -> UART0 -> USB0
Default Sysboot Pins SYSBOOT[4 : 0] == 0b11x00 SYSBOOT[2] HIGH == eMMC SYSBOOT[2] LOW == SD Card
SYSBOOT to config boot order must use very light pullups because boot config is latched at boot and then the pins a used for other purposes
SYSBOOT2 pulled high by default to boot eMMC. Manual jumper here to override and OPD can override.
SYSBOOT2

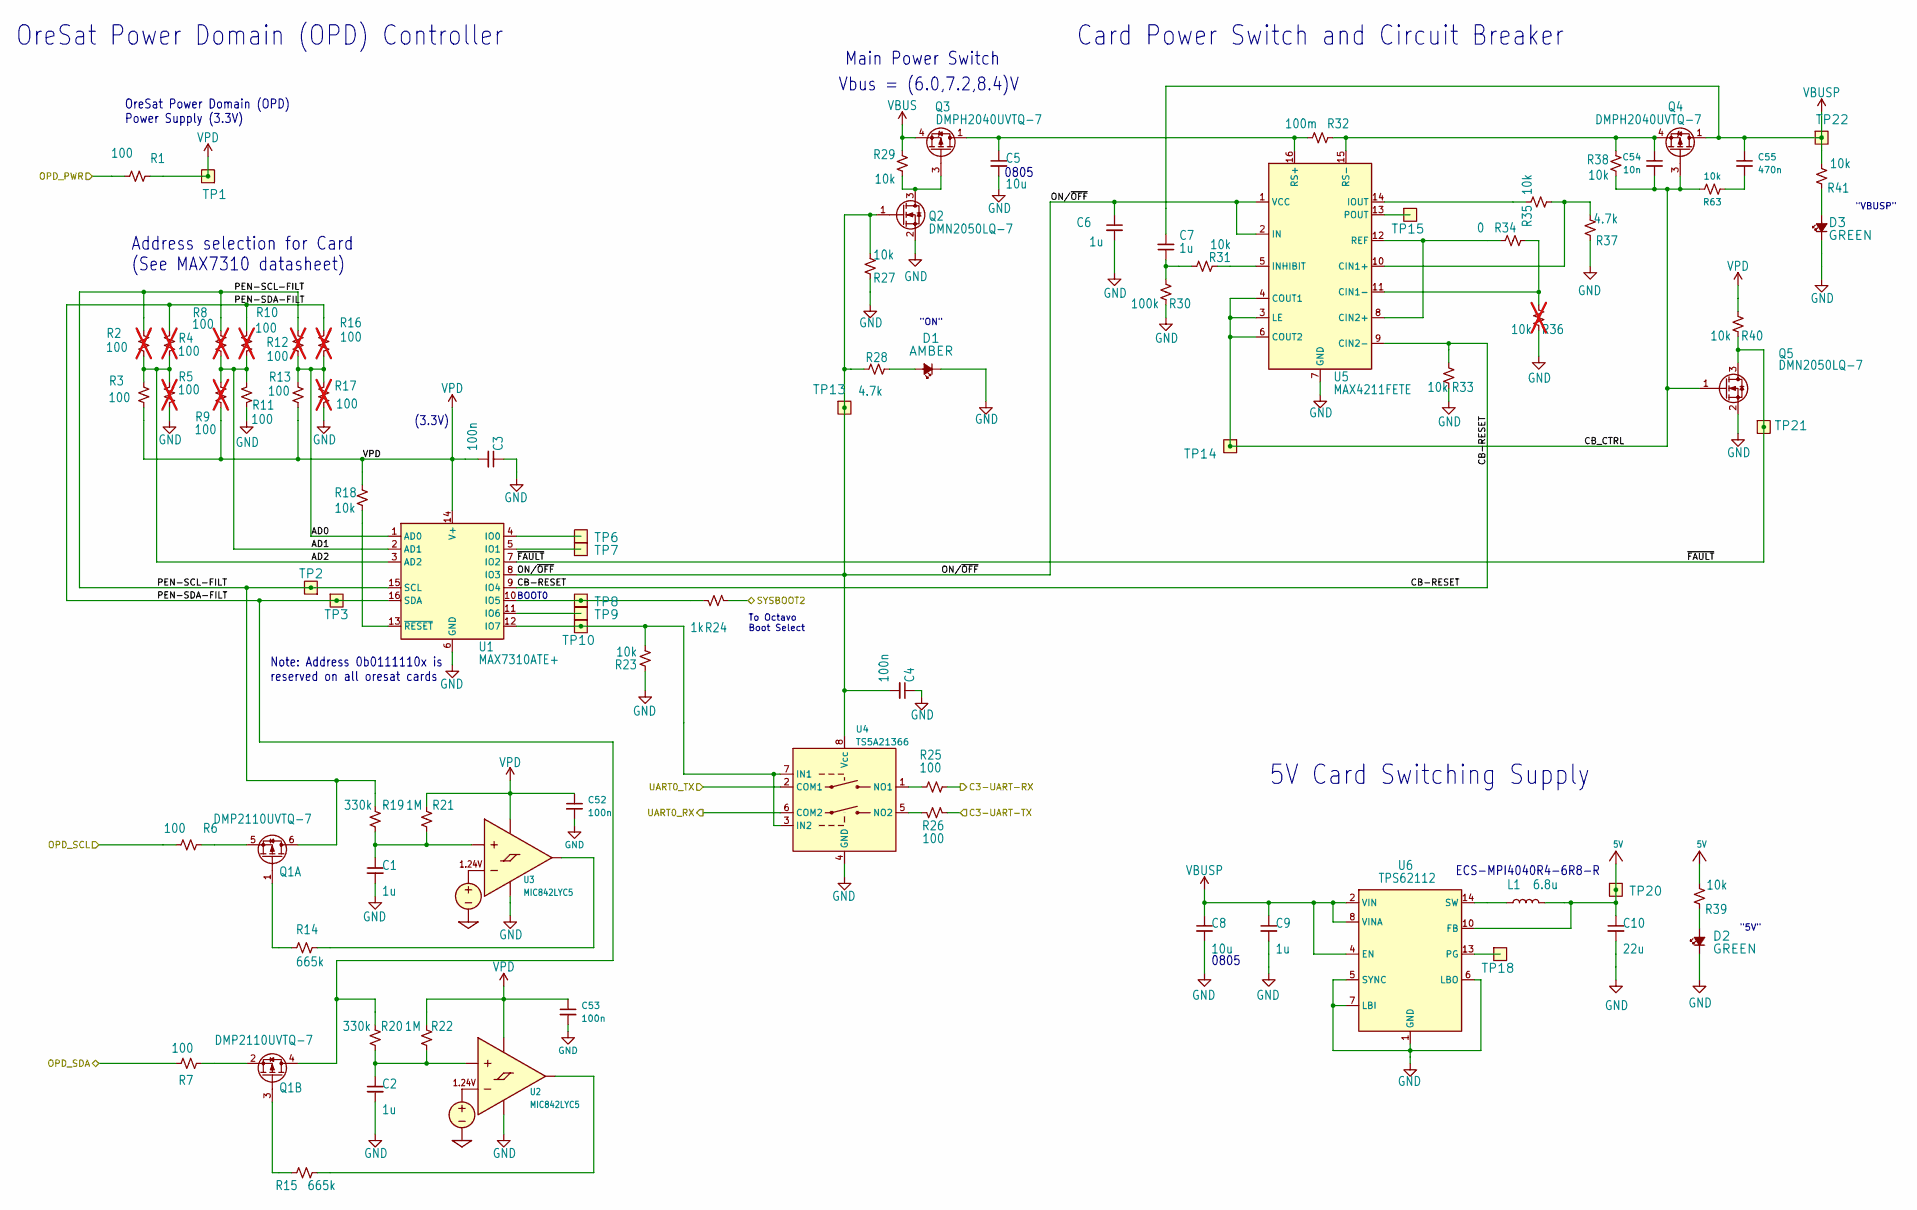
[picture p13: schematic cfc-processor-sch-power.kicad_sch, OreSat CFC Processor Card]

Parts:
C1, C2, C6, C7, C9: 1u; 0603-C-NOSILK; MPN GCM21BR71H105KA03L
C3, C4, C52, C53: 100n; 0603-C-NOSILK; MPN C0603C104K5RACAUTO
C5, C8: 10u; 0805-C-NOSILK; MPN GRT21BC71E106KE13K
C10: 22u; C_1210_3225Metric; MPN TMK325B7226KMHP
C54: 10n; 0603-C-NOSILK; MPN C0603C103J5RACAUTO
C55: 470n; 0603-C-NOSILK; MPN C0603C474K3RACAUTO
D1: AMBER; LED_0603_1608Metric; MPN 150060AS75000
D2, D3: GREEN; LED_0603_1608Metric; MPN 150060GS75000
L1: 6.8u; L_ECS-MPI4040; MPN ECS-MPI4040R4-6R8-R
Q1: DMP2110UVTQ-7; SOT-23-6; MPN DMP2110UVTQ-7
Q2, Q5: DMN2050LQ-7; SOT-23; MPN DMN2050LQ-7
Q3, Q4: DMPH2040UVTQ-7; TSOT-23-6; MPN DMPH2040UVTQ-7
R1, R3, R6, R7, R11, R13, R25, R26: 100; 0603-C-NOSILK; MPN RMCF0603FT100R
R2, R4, R5, R8, R9, R10, R12, R16, R17: 100; 0603-C-NOSILK; MPN RMCF0603FT100R; not fitted
R14, R15: 665k; 0603-C-NOSILK; MPN RMCF0603FT665K
R18, R23, R27, R29, R31, R33, R35, R38, R39, R40, R41, R63: 10k; 0603-C-NOSILK; MPN RMCF0603FT10K0
R19, R20: 330k; 0603-C-NOSILK; MPN RMCF0603FT330K
R21, R22: 1M; 0603-C-NOSILK; MPN RMCF0603FG1M00
R24: 1k; 0603-C-NOSILK; MPN RMCF0603FT1K00
R28, R37: 4.7k; 0603-C-NOSILK; MPN RMCF0603FT4K70
R30: 100k; 0603-C-NOSILK; MPN RMCF0603FT100K
R32: 100m; 1206-C; MPN CSR1206FTR100
R34: 0; 0603-C-NOSILK; MPN RMCF0603ZT0R00
R36: 10k; 0603-C-NOSILK; MPN RC1005F6653CS; not fitted
TP1, TP2, TP3, TP6, TP7, TP8, TP9, TP10, TP13, TP14, TP15, TP18, TP20, TP21, TP22: TEST-POINT; TestPoint-0.75mm-th
U1: MAX7310ATE+; QFN-16-1EP_4x4mm_P0.65mm_EP2.1x2.1mm; MPN MAX7310ATE+
U2, U3: MIC842LYC5; SOT-353_SC-70-5; MPN MIC842LYC5-TR
U4: TS5A21366; VSSOP-8_2.3x2mm_P0.5mm; MPN TS5A21366DCUR
U5: MAX4211FETE; QFN-16-1EP_4x4mm_P0.65mm_EP2.1x2.1mm; MPN MAX4211FETE
U6: TPS62112; Texas_RSA_VQFN-16-1EP_4x4mm_P0.65mm_EP2.7x2.7mm; MPN TPS62112RSAR

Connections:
5V: C10.1, L1.2, R39.2, TP20.1 (1_1), U6.10 (FB); also elsewhere on the board
/C3-UART-RX: R25.1; also elsewhere on the board
/C3-UART-TX: R26.2; also elsewhere on the board
/OPD_PWR: R1.1; also elsewhere on the board
/OPD_SCL: R6.1; also elsewhere on the board
/OPD_SDA: R7.1; also elsewhere on the board
/OSD3358: SIP C/UART-RX: U4.6 (COM2); also elsewhere on the board
/OSD3358: SIP C/UART-TX: U4.2 (COM1); also elsewhere on the board
/OSD3358: SIP D (BOOT)/SYSBOOT2: R24.2; also elsewhere on the board
/Power (OPD)/AD0: R12.2, R13.1, R16.2, R17.1, U1.1 (AD0)
/Power (OPD)/AD1: R8.2, R9.1, R10.2, R11.1, U1.2 (AD1)
/Power (OPD)/AD2: R2.2, R3.1, R4.2, R5.1, U1.3 (AD2)
/Power (OPD)/CB-RESET: R33.2, U1.9 (IO4), U5.9 (CIN2-)
/Power (OPD)/CB_CTRL: C54.2, Q4.3 (G), Q5.1 (G), R38.1, R63.2, TP14.1 (1_1), U5.3 (LE), U5.4 (COUT1), U5.6 (COUT2)
/Power (OPD)/ON/~OFF: C4.2, C6.1, Q2.1 (G), R27.2, R28.2, TP13.1 (1_1), U1.8 (IO3), U4.8 (Vcc), U5.1 (VCC), U5.2 (IN)
/Power (OPD)/PEN-SCL-FILT: Q1.6 (D), R2.1, R8.1, R12.1, R19.2, TP2.1 (1_1), U1.15 (SCL)
/Power (OPD)/PEN-SDA-FILT: Q1.4 (D), R4.1, R10.1, R16.1, R20.2, TP3.1 (1_1), U1.16 (SDA)
/Power (OPD)/~FAULT: Q5.3 (D), R40.1, TP21.1 (1_1), U1.7 (IO2)
GND: C1.2, C2.2, C3.1, C4.1, C5.2, C6.2, C8.2, C9.2, C10.2, C52.2, C53.2, D1.1 (K), D2.1 (K), D3.1 (K), Q2.2 (S), Q5.2 (S), R5.2, R11.2, R17.2, R23.1, R27.1, R30.1, R33.1, R36.1, R37.1, U1.6 (GND), U1.17 (GND), U2.2 (GND), U3.2 (GND), U4.4 (GND), U5.7 (GND), U5.17 (GND), U6.1 (GND), U6.5 (SYNC), U6.6 (LBO), U6.7 (LBI), U6.9 (GND), U6.11 (GND), U6.12 (GND), U6.16 (GND), U6.17 (GND); also elsewhere on the board
unnamed: C7.1, R30.2, R31.2
unnamed: C55.2, R63.1
unnamed: D1.2 (A), R28.1
unnamed: D2.2 (A), R39.1
unnamed: D3.2 (A), R41.1
unnamed: L1.1, U6.14 (SW), U6.15 (SW)
unnamed: Q1.1 (G), R14.2
unnamed: Q1.5 (S), R6.2
unnamed: Q1.3 (G), R15.2
unnamed: Q1.2 (S), R7.2
unnamed: Q2.3 (D), Q3.3 (G), R29.1
unnamed: C54.1, Q4.4 (S), R32.2, R38.2, U5.15 (RS-)
unnamed: TP6.1 (1_1), U1.4 (IO0)
unnamed: TP7.1 (1_1), U1.5 (IO1)
unnamed: R24.1, TP8.1 (1_1), U1.10 (IO5)
unnamed: TP9.1 (1_1), U1.11 (IO6)
unnamed: R23.2, TP10.1 (1_1), U1.12 (IO7), U4.3 (IN2), U4.7 (IN1)
unnamed: R18.1, U1.13 (~RESET)
unnamed: C2.1, R20.1, R22.1, U2.1 (INP)
unnamed: R15.1, U2.4 (OUT)
unnamed: C1.1, R19.1, R21.1, U3.1 (INP)
unnamed: R14.1, U3.4 (OUT)
unnamed: R25.2, U4.1 (NO1)
unnamed: R26.1, U4.5 (NO2)
unnamed: R35.1, R37.2, U5.10 (CIN1+)
unnamed: R34.1, R36.2, U5.11 (CIN1-)
unnamed: R34.2, U5.8 (CIN2+), U5.12 (REF)
unnamed: R31.1, U5.5 (INHIBIT)
unnamed: R35.2, U5.14 (IOUT)
unnamed: TP15.1 (1_1), U5.13 (POUT)
unnamed: C5.1, Q3.1 (D), Q3.2 (D), Q3.5 (D), Q3.6 (D), R32.1, U5.16 (RS+)
unnamed: TP18.1 (1_1), U6.13 (PG)
VBUS: Q3.4 (S), R29.2; also elsewhere on the board
VBUSP: C7.2, C8.1, C9.1, C55.1, Q4.1 (D), Q4.2 (D), Q4.5 (D), Q4.6 (D), R41.2, TP22.1 (1_1), U6.2 (VIN), U6.3 (VIN), U6.4 (EN), U6.8 (VINA)
VPD: C3.2, C52.1, C53.1, R1.2, R3.2, R9.2, R13.2, R18.2, R21.2, R22.2, R40.2, TP1.1 (1_1), U1.14 (V+), U2.5 (VDD), U3.5 (VDD)

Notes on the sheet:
0805
Card Power Switch and Circuit Breaker
BOOT0
Main Power Switch
OreSat Power Domain (OPD) Controller
"ON"
"5V"
ECS-MPI4040R4-6R8-R
(3.3V)
OreSat Power Domain (OPD) Power Supply (3.3V)
Address selection for Card (See MAX7310 datasheet)
To Octavo Boot Select
Vbus = (6.0,7.2,8.4)V
"VBUSP"
5V Card Switching Supply
Note: Address 0b0111110x is reserved on all oresat cards

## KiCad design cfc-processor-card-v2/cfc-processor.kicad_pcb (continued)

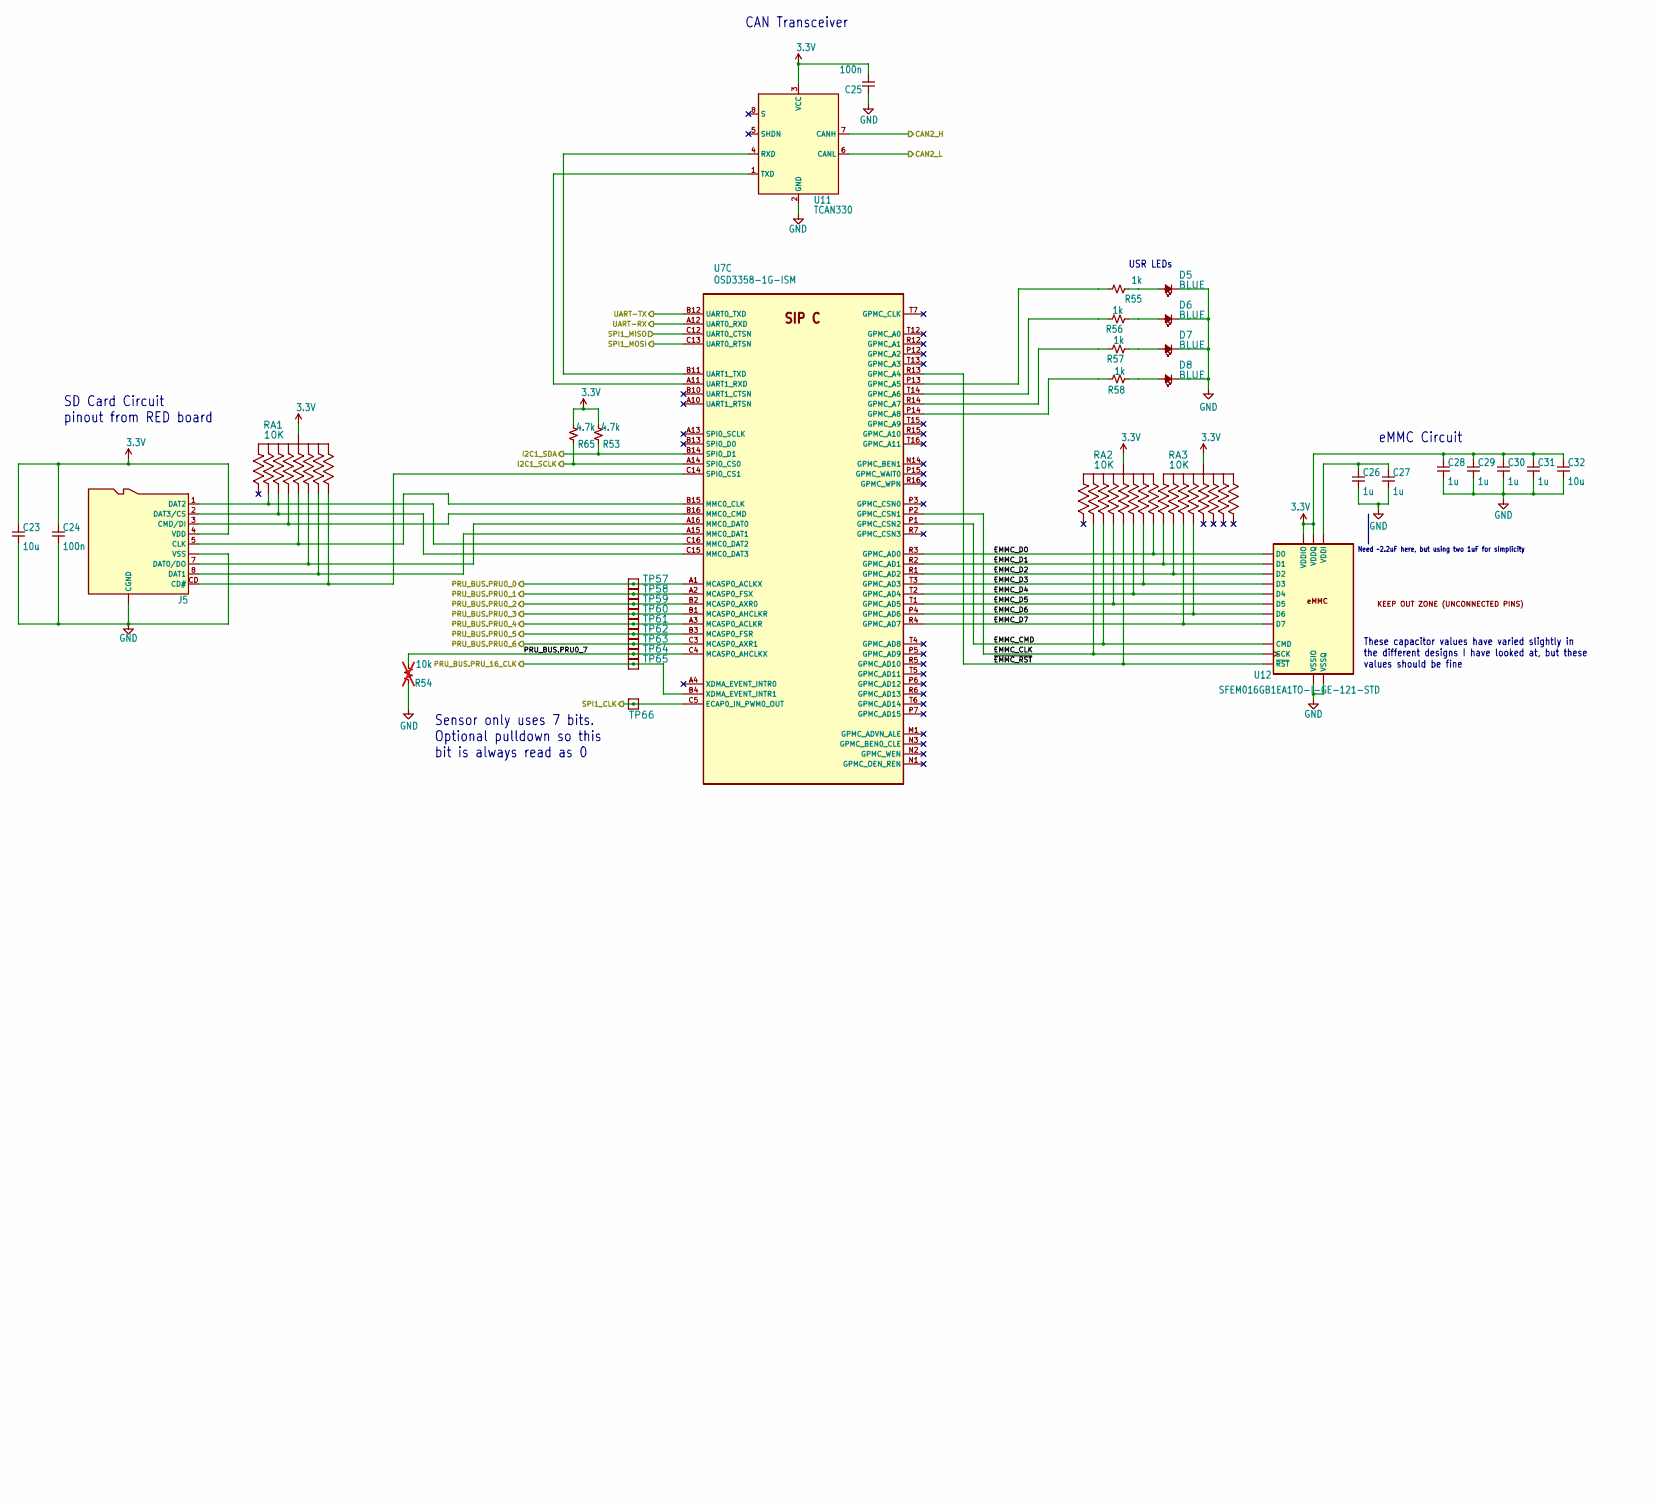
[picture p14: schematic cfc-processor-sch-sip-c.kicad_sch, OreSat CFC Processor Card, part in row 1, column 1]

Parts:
C23, C32: 10u; 0805-C-NOSILK; MPN GRT21BC71E106KE13K
C24, C25: 100n; 0603-C-NOSILK; MPN C0603C104K5RACAUTO
C26, C27, C28, C29, C30, C31: 1u; 0603-C-NOSILK; MPN GCM21BR71H105KA03L
D5, D6, D7, D8: BLUE; LED_0603_1608Metric; MPN 150060BS75000
J5: DM3BT-DSF-PEJS; J-Hirose-DM3BT-DSF-PEJS; MPN DM3BT-DSF-PEJS
R53, R65: 4.7k; 0603-C-NOSILK; MPN RMCF0603FT4K70
R54: 10k; 0603-C-NOSILK; not fitted
R55, R56, R57, R58: 1k; 0603-C-NOSILK; MPN RMCF0603FT1K00
RA1, RA2, RA3: 10K; ARRAY_EXBA-M; MPN EXB-A10P103J
TP57, TP58, TP59, TP60, TP61, TP62, TP63, TP64, TP65, TP66: TEST-POINT; 2MM-TEST-POINT
U7: OSD3358-1G-ISM; U-Octavo-OSD335X-BGA-256; MPN OSD3358-1G-ISM
U11: TCAN330; SOT-23-8; MPN TCAN330GDCNT
U12: SFEM016GB1EA1TO-I-GE-121-STD; BGA-153(11.5X13)(EMMC-BA); MPN SFEM016GB1EA1TO-I-GE-121-STD

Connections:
3.3V: C23.1, C24.1, C25.2, C28.1, C29.1, C30.1, C31.1, C32.1, J5.4 (VDD), R53.2, R65.2, RA1.5 (55), RA1.10 (55), RA2.5 (55), RA2.10 (55), RA3.5 (55), RA3.10 (55), U11.3 (VCC), U12.C6 (VDDQ), U12.E6 (VDDIO), U12.F5 (VDDIO), U12.J10 (VDDIO), U12.K9 (VDDIO), U12.M4 (VDDQ), U12.N4 (VDDQ), U12.P3 (VDDQ), U12.P5 (VDDQ); also elsewhere on the board
/CAN2_H: U11.7 (CANH); also elsewhere on the board
/CAN2_L: U11.6 (CANL); also elsewhere on the board
/Deserializer/PRU_BUS.PRU0_0: TP57.1 (1_1), U7.A1 (MCASP0_ACLKX); also elsewhere on the board
/Deserializer/PRU_BUS.PRU0_1: TP58.1 (1_1), U7.A2 (MCASP0_FSX); also elsewhere on the board
/Deserializer/PRU_BUS.PRU0_2: TP59.1 (1_1), U7.B2 (MCASP0_AXR0); also elsewhere on the board
/Deserializer/PRU_BUS.PRU0_3: TP60.1 (1_1), U7.B1 (MCASP0_AHCLKR); also elsewhere on the board
/Deserializer/PRU_BUS.PRU0_4: TP61.1 (1_1), U7.A3 (MCASP0_ACLKR); also elsewhere on the board
/Deserializer/PRU_BUS.PRU0_5: TP62.1 (1_1), U7.B3 (MCASP0_FSR); also elsewhere on the board
/Deserializer/PRU_BUS.PRU0_6: TP63.1 (1_1), U7.C3 (MCASP0_AXR1); also elsewhere on the board
/Deserializer/PRU_BUS.PRU_16_CLK: TP65.1 (1_1), U7.B4 (XDMA_EVENT_INTR1); also elsewhere on the board
/I2C1_CLK: R65.1, U7.A14 (SPI0_CS0); also elsewhere on the board
/I2C1_SDA: R53.1, U7.B14 (SPI0_D1); also elsewhere on the board
/OSD3358: SIP C/EMMC_CLK: RA2.9 (99), U7.P2 (GPMC_CSN1), U12.M6 (SCK)
/OSD3358: SIP C/EMMC_CMD: RA2.2 (22), U7.P1 (GPMC_CSN2), U12.M5 (CMD)
/OSD3358: SIP C/EMMC_D0: RA2.6 (66), U7.R3 (GPMC_AD0), U12.A3 (D0)
/OSD3358: SIP C/EMMC_D1: RA3.1 (11), U7.R2 (GPMC_AD1), U12.A4 (D1)
/OSD3358: SIP C/EMMC_D2: RA3.9 (99), U7.R1 (GPMC_AD2), U12.A5 (D2)
/OSD3358: SIP C/EMMC_D3: RA2.4 (44), U7.T3 (GPMC_AD3), U12.B2 (D3)
/OSD3358: SIP C/EMMC_D4: RA2.7 (77), U7.T2 (GPMC_AD4), U12.B3 (D4)
/OSD3358: SIP C/EMMC_D5: RA2.8 (88), U7.T1 (GPMC_AD5), U12.B4 (D5)
/OSD3358: SIP C/EMMC_D6: RA3.8 (88), U7.P4 (GPMC_AD6), U12.B5 (D6)
/OSD3358: SIP C/EMMC_D7: RA3.2 (22), U7.R4 (GPMC_AD7), U12.B6 (D7)
/OSD3358: SIP C/PRU_BUS.PRU0_7: R54.2, TP64.1 (1_1), U7.C4 (MCASP0_AHCLKX)
/OSD3358: SIP C/UART-RX: U7.A12 (UART0_RXD); also elsewhere on the board
/OSD3358: SIP C/UART-TX: U7.B12 (UART0_TXD); also elsewhere on the board
/OSD3358: SIP C/~EMMC_RST: RA2.3 (33), U7.R13 (GPMC_A4), U12.K5 (~RST)
/SPI1_CLK: TP66.1 (1_1), U7.C5 (ECAP0_IN_PWM0_OUT); also elsewhere on the board
/SPI1_MISO: U7.C12 (UART0_CTSN); also elsewhere on the board
/SPI1_MOSI: U7.C13 (UART0_RTSN); also elsewhere on the board
GND: C23.2, C24.2, C25.1, C26.2, C27.2, C28.2, C29.2, C30.2, C31.2, C32.2, D5.1 (K), D6.1 (K), D7.1 (K), D8.1 (K), J5.6 (VSS), J5.CGND1 (CGND), J5.CGND2 (CGND), J5.CGND3 (CGND), J5.CGND4 (CGND), J5.CGND5 (CGND), J5.CGND6 (CGND), J5.GND (VSS), R54.1, U11.2 (GND), U12.A6 (VSSIO), U12.C4 (VSSQ), U12.E7 (VSSIO), U12.G5 (VSSIO), U12.H10 (VSSIO), U12.J5 (VSSIO), U12.K8 (VSSIO), U12.N2 (VSSQ), U12.N5 (VSSQ), U12.P4 (VSSQ), U12.P6 (VSSQ); also elsewhere on the board
unnamed: D5.2 (A), R55.2
unnamed: D6.2 (A), R56.2
unnamed: D7.2 (A), R57.2
unnamed: D8.2 (A), R58.2
unnamed: J5.CD (CD#), RA1.6 (66), U7.C14 (SPI0_CS1)
unnamed: J5.5 (CLK), RA1.3 (33), U7.B15 (MMC0_CLK)
unnamed: J5.3 (CMD/DI), RA1.8 (88), U7.B16 (MMC0_CMD)
unnamed: J5.7 (DAT0/DO), RA1.7 (77), U7.A16 (MMC0_DAT0)
unnamed: J5.8 (DAT1), RA1.4 (44), U7.A15 (MMC0_DAT1)
unnamed: J5.1 (DAT2), RA1.9 (99), U7.C16 (MMC0_DAT2)
unnamed: J5.2 (DAT3/CS), RA1.2 (22), U7.C15 (MMC0_DAT3)
unnamed: R55.1, U7.P13 (GPMC_A5)
unnamed: R56.1, U7.T14 (GPMC_A6)
unnamed: R57.1, U7.R14 (GPMC_A7)
unnamed: R58.1, U7.P14 (GPMC_A8)
unnamed: U7.B11 (UART1_TXD), U11.4 (RXD)
unnamed: U7.A11 (UART1_RXD), U11.1 (TXD)
unnamed: C26.1, C27.1, U12.C2 (VDDI)

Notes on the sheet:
USR LEDs
Sensor only uses 7 bits. Optional pulldown so this bit is always read as 0
Need ~2.2uF here, but using two 1uF for simplicity
SD Card Circuit pinout from RED board
1.2
These capacitor values have varied slightly in the different designs I have looked at, but these values should be fine
CAN Transceiver
eMMC Circuit

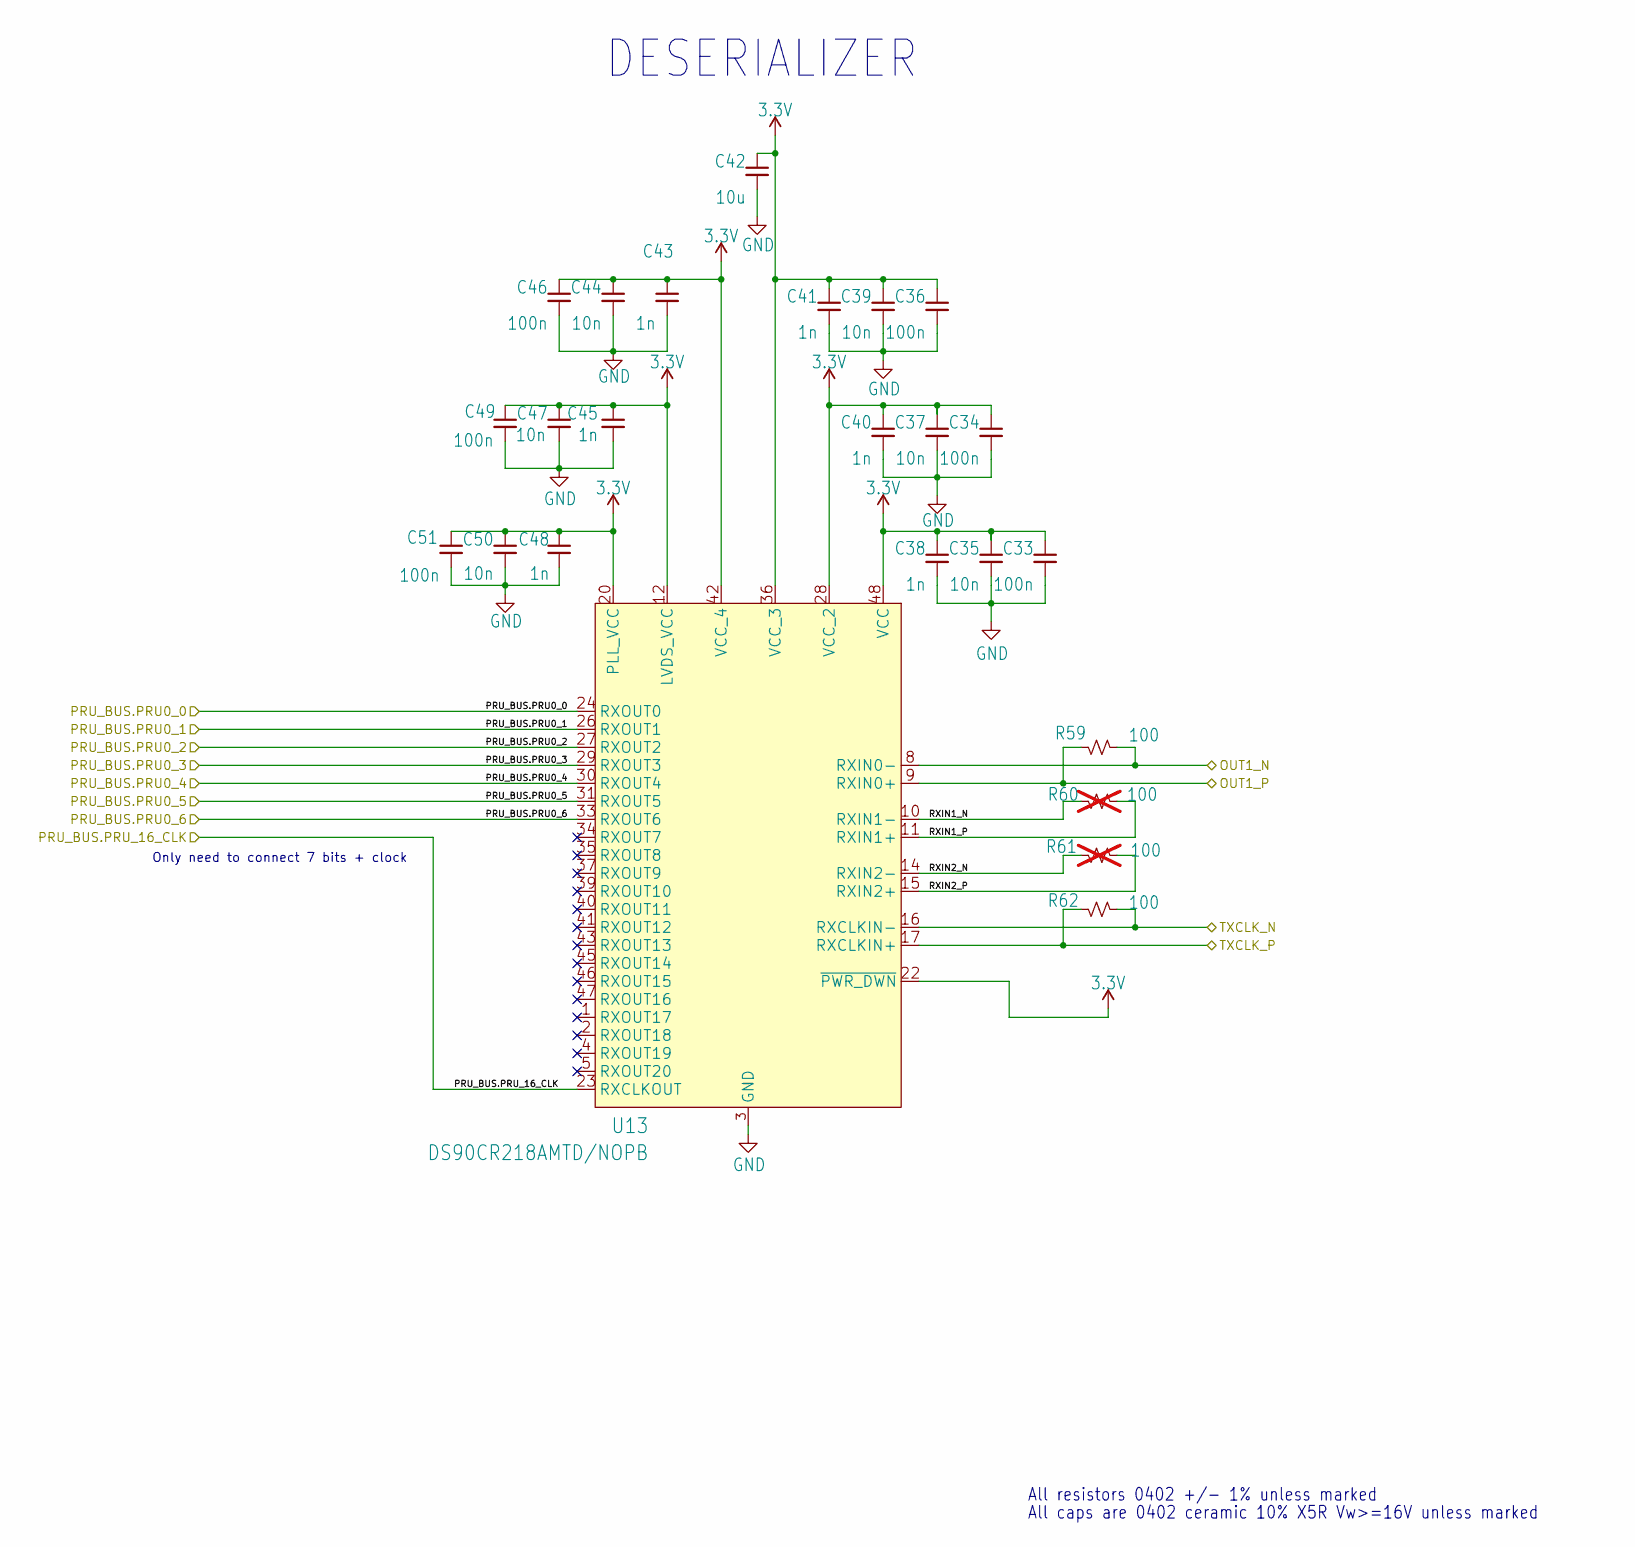
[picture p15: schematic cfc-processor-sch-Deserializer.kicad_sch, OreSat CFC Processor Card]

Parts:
C33, C34, C36, C46, C49, C51: 100n; 0402-C-NOSILK; MPN C0402C104K4RECAUTO
C35, C37, C39, C44, C47, C50: 10n; 0402-C-NOSILK; MPN GXT155R71E103KE01D
C38, C40, C41, C43, C45, C48: 1n; 0402-C-NOSILK; MPN C0402C102J3GACAUTO
C42: 10u; 0805-C-NOSILK; MPN GRT21BC71E106KE13K
R59, R62: 100; 0402-C-NOSILK; MPN RMCF0402FT100R
R60, R61: 100; 0402-C-NOSILK; MPN RC0201FR-07100RL; not fitted
U13: DS90CR218AMTD/NOPB; MTD48_TEX-L; MPN DS90CR218AMTD/NOPB

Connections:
3.3V: C33.1, C34.1, C35.1, C36.1, C37.1, C38.1, C39.1, C40.1, C41.1, C42.1, C43.1, C44.1, C45.1, C46.1, C47.1, C48.1, C49.1, C50.1, C51.1, U13.12 (LVDS_VCC), U13.20 (PLL_VCC), U13.22 (~PWR_DWN), U13.28 (VCC_2), U13.36 (VCC_3), U13.42 (VCC_4), U13.48 (VCC); also elsewhere on the board
/Deserializer/PRU_BUS.PRU0_0: U13.24 (RXOUT0); also elsewhere on the board
/Deserializer/PRU_BUS.PRU0_1: U13.26 (RXOUT1); also elsewhere on the board
/Deserializer/PRU_BUS.PRU0_2: U13.27 (RXOUT2); also elsewhere on the board
/Deserializer/PRU_BUS.PRU0_3: U13.29 (RXOUT3); also elsewhere on the board
/Deserializer/PRU_BUS.PRU0_4: U13.30 (RXOUT4); also elsewhere on the board
/Deserializer/PRU_BUS.PRU0_5: U13.31 (RXOUT5); also elsewhere on the board
/Deserializer/PRU_BUS.PRU0_6: U13.33 (RXOUT6); also elsewhere on the board
/Deserializer/PRU_BUS.PRU_16_CLK: U13.23 (RXCLKOUT); also elsewhere on the board
/Deserializer/RXIN1_N: R60.2, U13.10 (RXIN1-)
/Deserializer/RXIN1_P: R60.1, U13.11 (RXIN1+)
/Deserializer/RXIN2_N: R61.2, U13.14 (RXIN2-)
/Deserializer/RXIN2_P: R61.1, U13.15 (RXIN2+)
/OUT1_N: R59.2, U13.8 (RXIN0-); also elsewhere on the board
/OUT1_P: R59.1, U13.9 (RXIN0+); also elsewhere on the board
/TXCLK_N: R62.1, U13.16 (RXCLKIN-); also elsewhere on the board
/TXCLK_P: R62.2, U13.17 (RXCLKIN+); also elsewhere on the board
GND: C33.2, C34.2, C35.2, C36.2, C37.2, C38.2, C39.2, C40.2, C41.2, C42.2, C43.2, C44.2, C45.2, C46.2, C47.2, C48.2, C49.2, C50.2, C51.2, U13.3 (GND), U13.7 (GND), U13.13 (GND), U13.18 (GND), U13.19 (GND), U13.21 (GND), U13.25 (GND), U13.32 (GND), U13.38 (GND), U13.44 (GND); also elsewhere on the board

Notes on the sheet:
All caps are 0402 ceramic 10% X5R Vw>=16V unless marked
All resistors 0402 +/- 1% unless marked
Only need to connect 7 bits + clock
DESERIALIZER

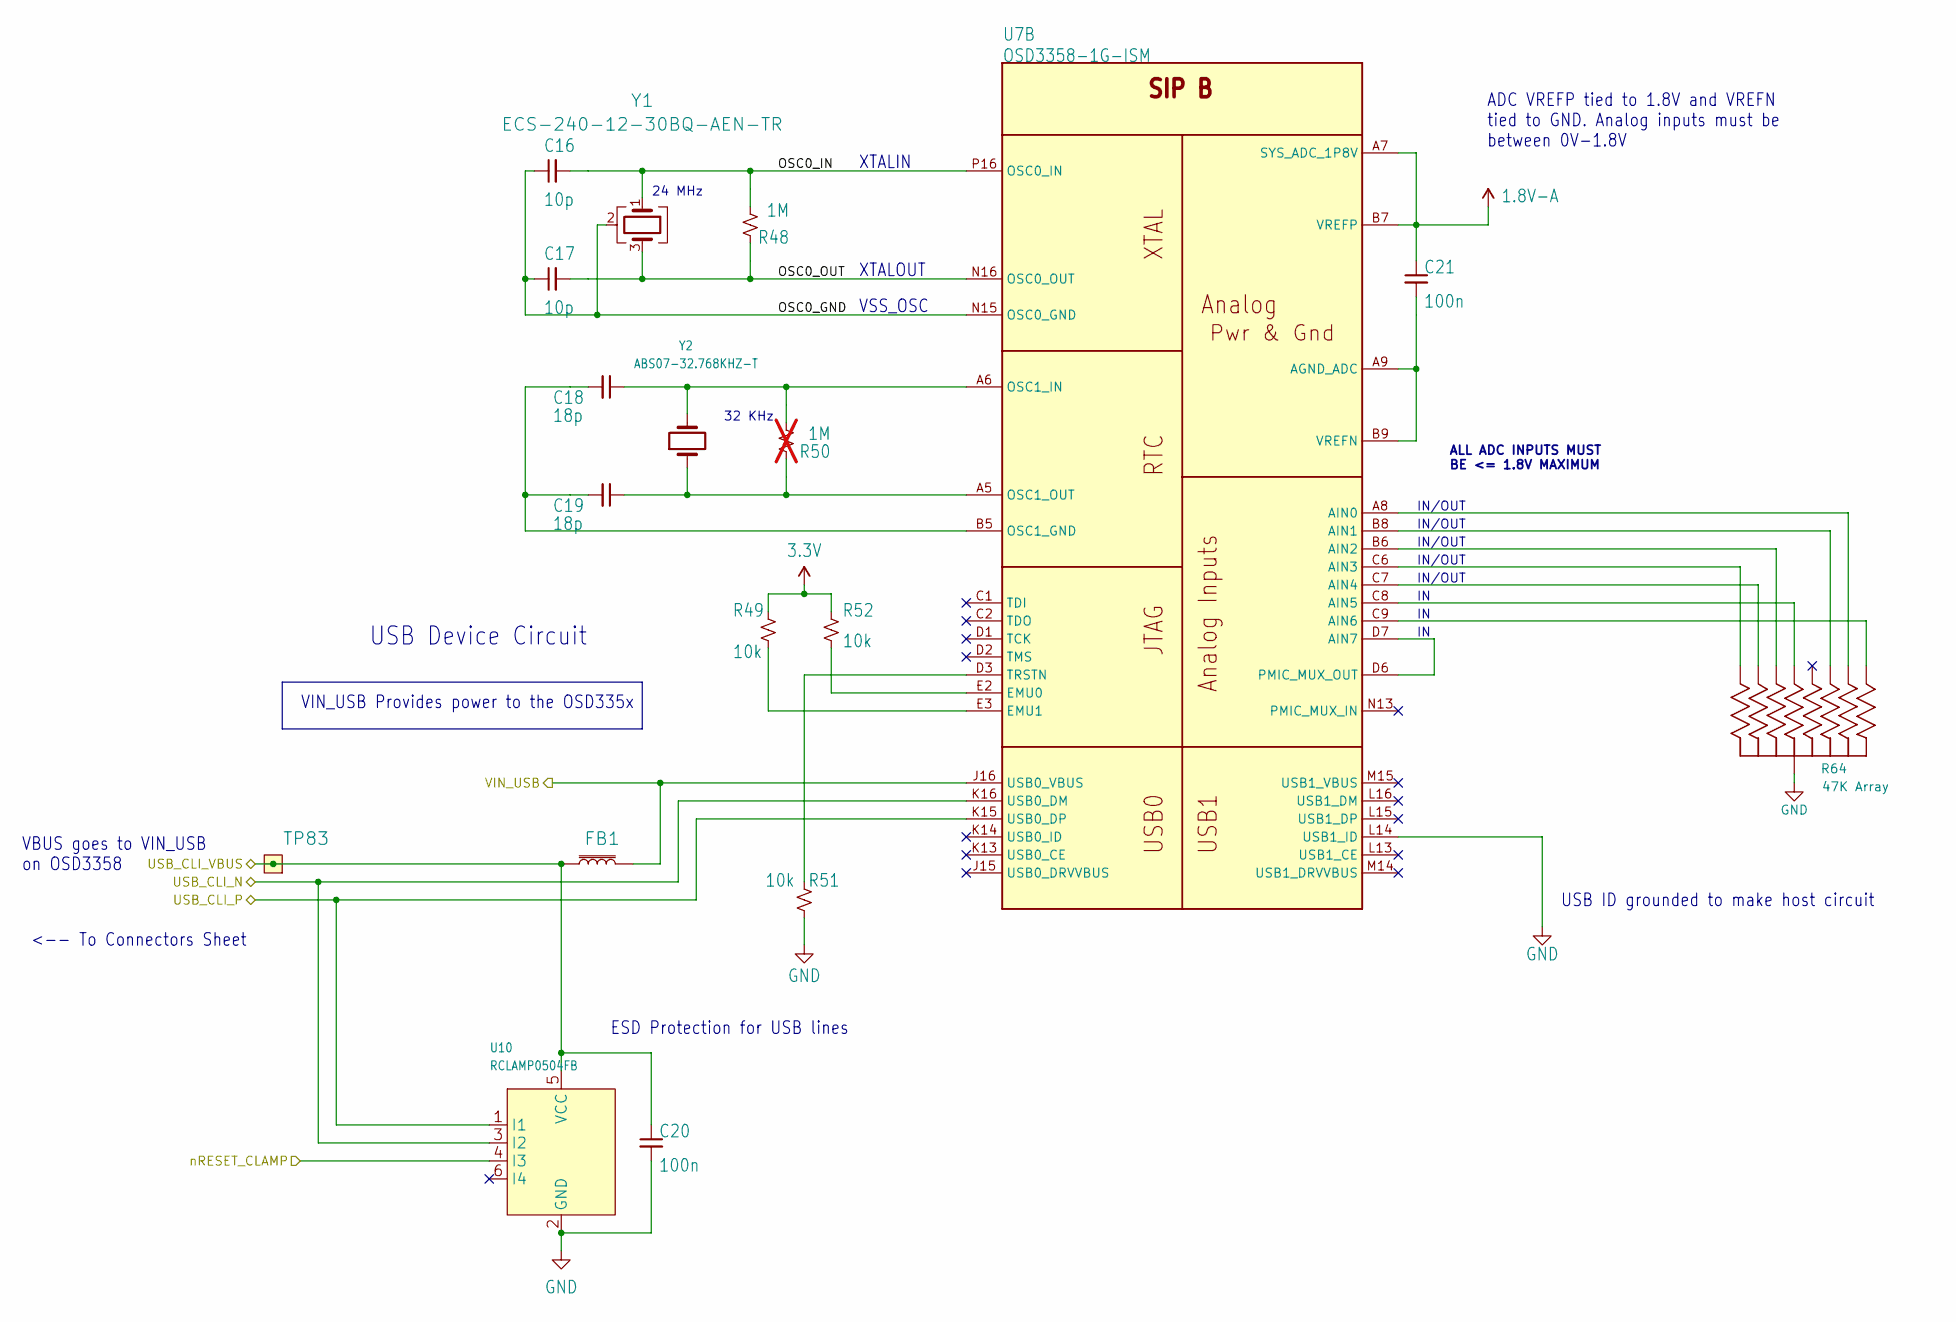
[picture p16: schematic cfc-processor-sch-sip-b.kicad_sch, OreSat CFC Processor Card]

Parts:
C16, C17: 10p; 0603-C-NOSILK; MPN C0603C100J1GACAUTO
C18, C19: 18p; 0603-C-NOSILK; MPN C0603C180J1GACAUTO
C20, C21: 100n; 0603-C-NOSILK; MPN C0603C104K5RACAUTO
FB1: BLM18KG300JH1D; L_0603_1608Metric; MPN BLM18KG300JH1D
R48: 1M; 0603-C-NOSILK; MPN RMCF0603FG1M00
R49, R51, R52: 10k; 0603-C-NOSILK; MPN RMCF0603FT10K0
R50: 1M; 0603-C-NOSILK; not fitted
R64: 47K Array; ARRAY_EXBA-M; MPN EXB-A10P473J
TP83: TEST-POINT; TestPoint-0.75mm-th
U7: OSD3358-1G-ISM; U-Octavo-OSD335X-BGA-256; MPN OSD3358-1G-ISM
U10: RCLAMP0504FB; SC70-6; MPN RCLAMP0504FBTCT
Y1: ECS-240-12-30BQ-AEN-TR; CRYSTAL-5X3.2-4SMD; MPN ECS-240-12-30BQ-AEN-TR
Y2: ABS07-32.768KHZ-T; CRYSTAL_3.2X1.5; MPN ABS07-32.768KHZ-T

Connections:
1.8V-A: C21.1, U7.A7 (SYS_ADC_1P8V), U7.B7 (VREFP)
3.3V: R49.2, R52.2; also elsewhere on the board
/OSD3358: SIP A (PWR)/NRESET: U10.4 (I3); also elsewhere on the board
/OSD3358: SIP A (PWR)/VIN_USB: FB1.2, U7.J16 (USB0_VBUS); also elsewhere on the board
/OSD3358: SIP B/OSC0_GND: C16.1, C17.1, U7.N15 (OSC0_GND), Y1.2 (G), Y1.4 (G)
/OSD3358: SIP B/OSC0_IN: C16.2, R48.2, U7.P16 (OSC0_IN), Y1.1
/OSD3358: SIP B/OSC0_OUT: C17.2, R48.1, U7.N16 (OSC0_OUT), Y1.3
/OSD3358: SIP B/USB_CLI_N: U7.K16 (USB0_DM), U10.3 (I2); also elsewhere on the board
/OSD3358: SIP B/USB_CLI_P: U7.K15 (USB0_DP), U10.1 (I1); also elsewhere on the board
/OSD3358: SIP B/USB_CLI_VBUS: C20.1, FB1.1, TP83.1 (1_1), U10.5 (VCC); also elsewhere on the board
GND: C20.2, R51.1, R64.5 (55), R64.10 (55), U7.L14 (USB1_ID), U10.2 (GND); also elsewhere on the board
unnamed: R64.1 (11), U7.C9 (AIN6)
unnamed: R64.2 (22), U7.B8 (AIN1)
unnamed: R64.3 (33), U7.C8 (AIN5)
unnamed: R64.4 (44), U7.C7 (AIN4)
unnamed: R64.6 (66), U7.C6 (AIN3)
unnamed: R64.7 (77), U7.B6 (AIN2)
unnamed: R64.9 (99), U7.A8 (AIN0)
unnamed: C21.2, U7.A9 (AGND_ADC), U7.B9 (VREFN)
unnamed: U7.D6 (PMIC_MUX_OUT), U7.D7 (AIN7)
unnamed: R52.1, U7.E2 (EMU0)
unnamed: R49.1, U7.E3 (EMU1)
unnamed: C18.2, C19.2, U7.B5 (OSC1_GND)
unnamed: C18.1, R50.2, U7.A6 (OSC1_IN), Y2.2
unnamed: C19.1, R50.1, U7.A5 (OSC1_OUT), Y2.1
unnamed: R51.2, U7.D3 (TRSTN)

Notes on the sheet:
XTALOUT
IN/OUT
<-- To Connectors Sheet
USB ID grounded to make host circuit
VSS_OSC
ADC VREFP tied to 1.8V and VREFN tied to GND. Analog inputs must be between 0V-1.8V
VBUS goes to VIN_USB on OSD3358
USB Device Circuit
VIN_USB Provides power to the OSD335x
ESD Protection for USB lines
24 MHz
ALL ADC INPUTS MUST BE <= 1.8V MAXIMUM
32 KHz
XTALIN

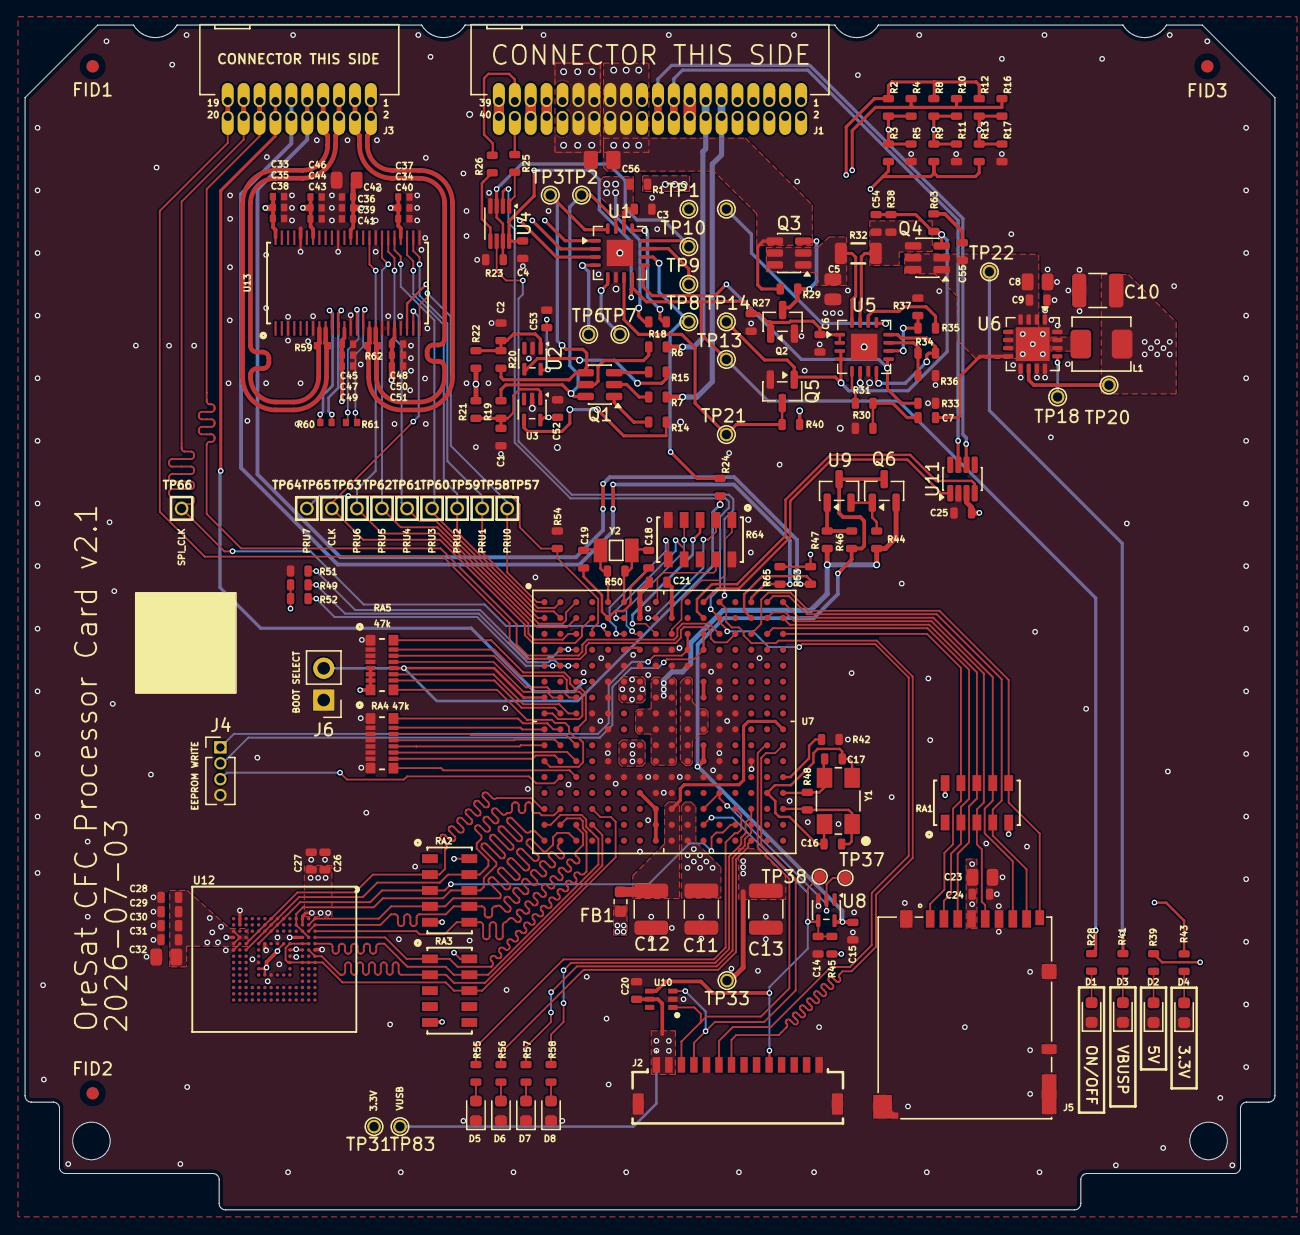
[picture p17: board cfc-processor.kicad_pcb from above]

Board: 4 copper layers, 99.8 x 94.6 mm, 196 parts (0 on the bottom side), 165 nets.

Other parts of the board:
PCB1: ORESAT-CARD-V1.3-GENERIC-0RF

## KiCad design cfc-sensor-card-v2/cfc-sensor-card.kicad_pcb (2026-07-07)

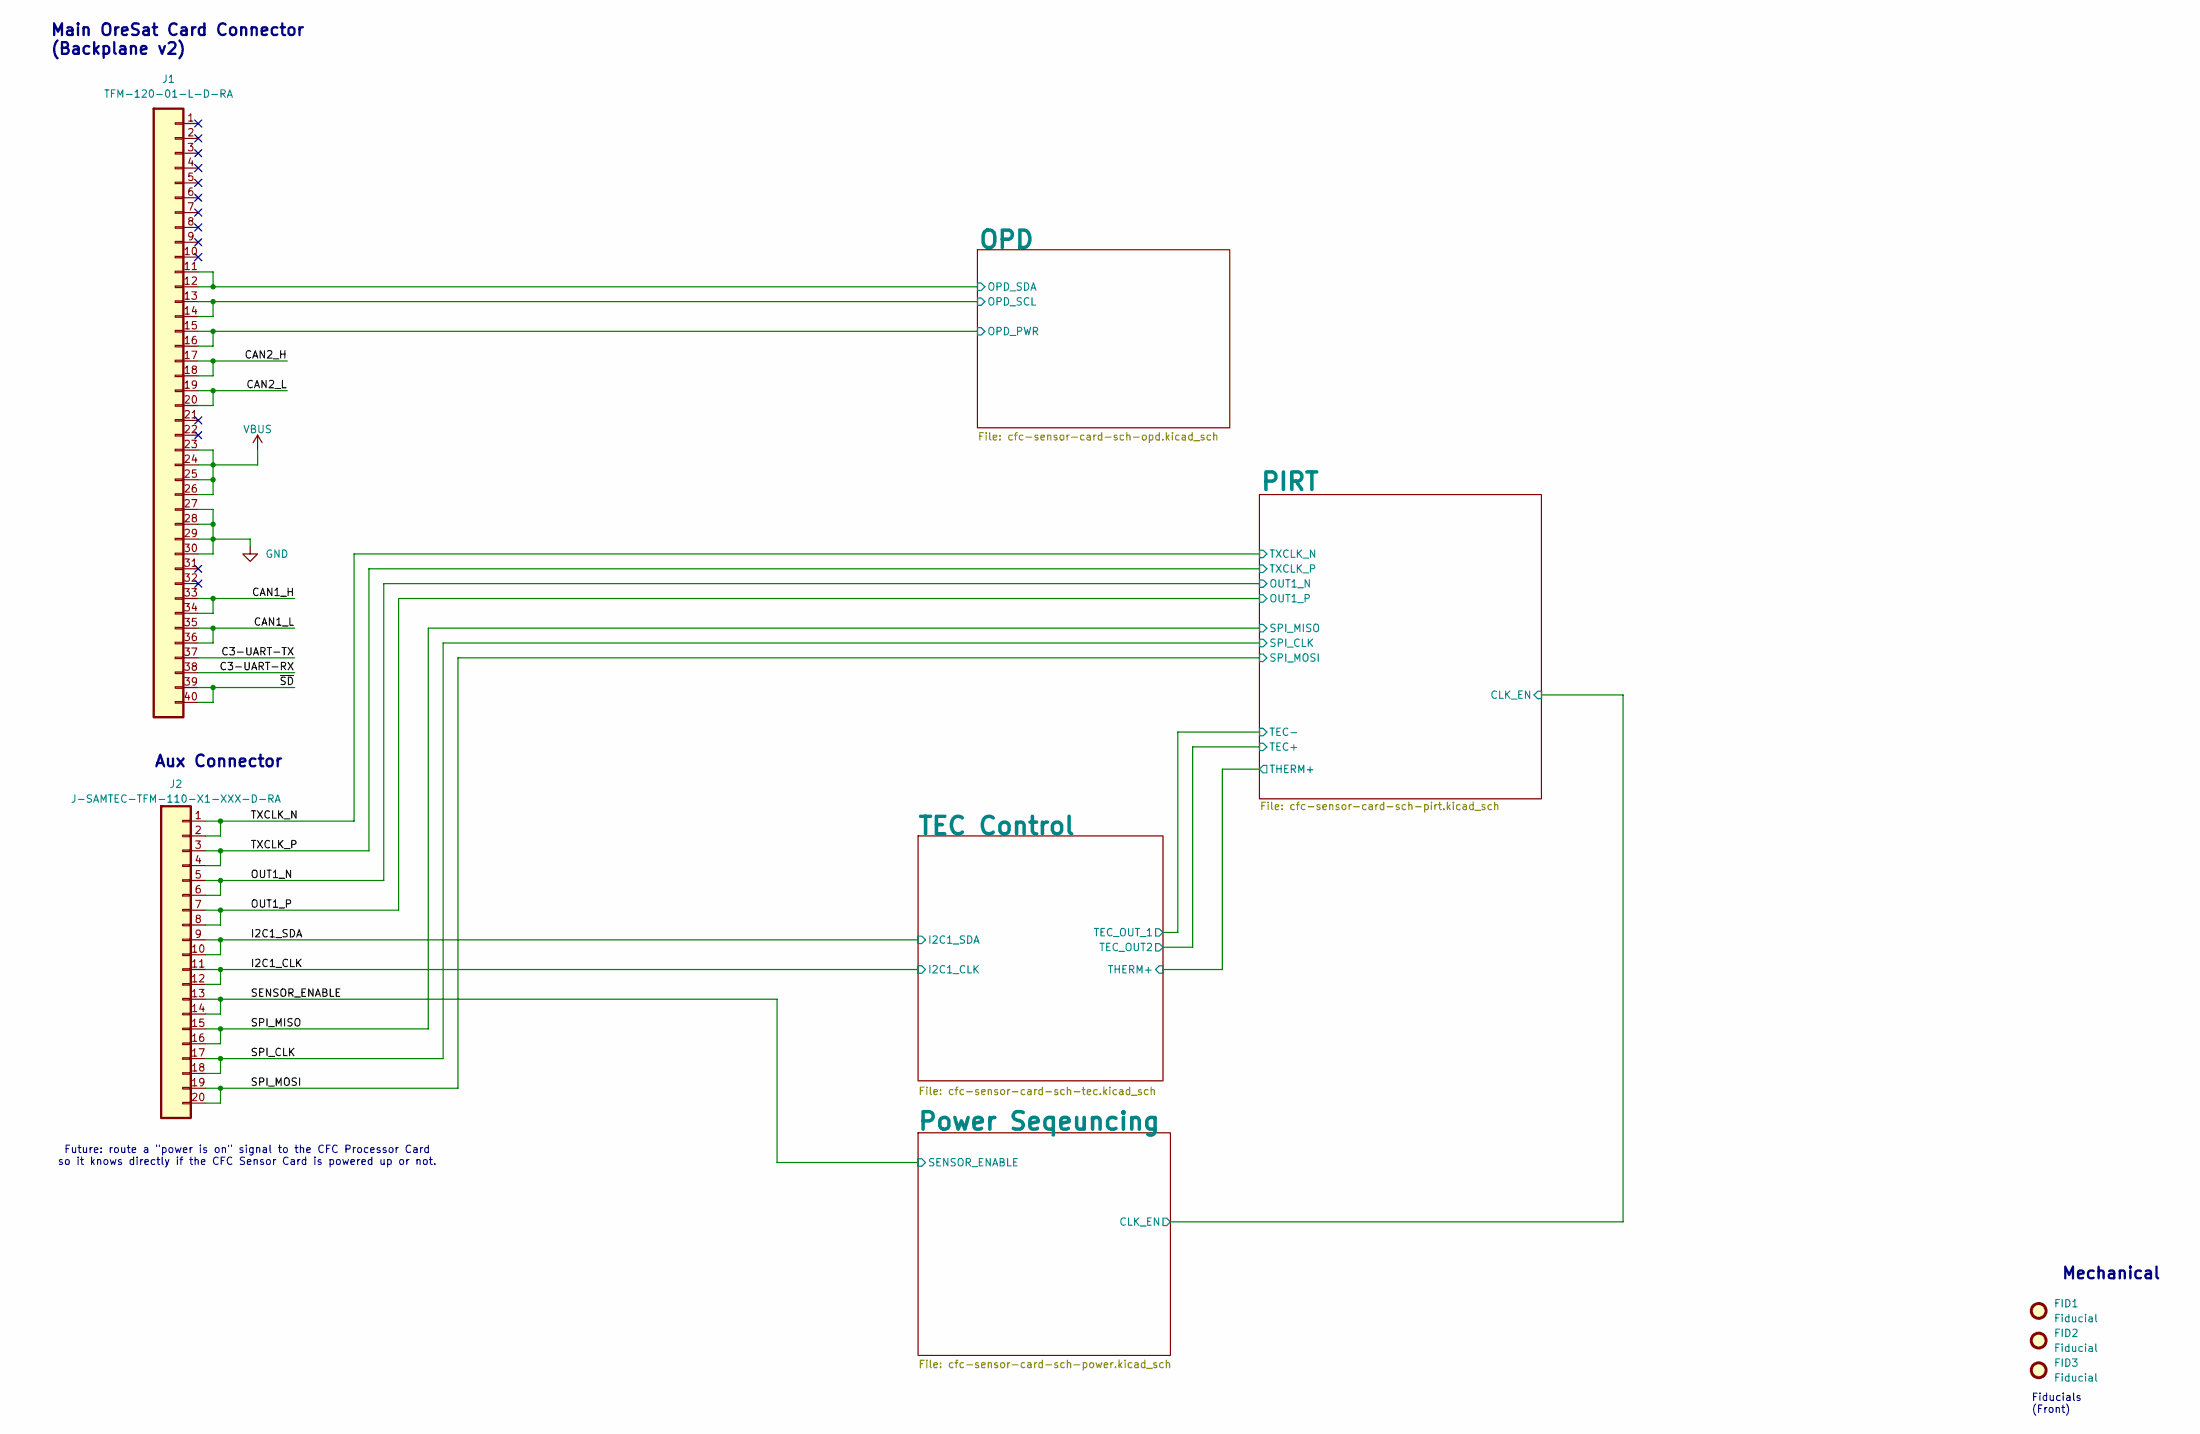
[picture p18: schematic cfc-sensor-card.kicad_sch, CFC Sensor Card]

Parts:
FID1, FID2, FID3: Fiducial; Fiducial_1mm_Mask2mm
J1: TFM-120-01-L-D-RA; J-SAMTEC-TFM-120-X1-XXX-D-RA; MPN TFM-120-01-L-D-RA
J2: J-SAMTEC-TFM-110-X1-XXX-D-RA; MPN TFM-110-01-L-D-RA

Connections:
/C3-UART-RX: J1.38
/C3-UART-TX: J1.37
/CAN1_H: J1.33, J1.34
/CAN1_L: J1.35, J1.36
/CAN2_H: J1.17, J1.18
/CAN2_L: J1.19, J1.20
/I2C1_CLK: J2.11, J2.12; also elsewhere on the board
/I2C1_SDA: J2.9, J2.10; also elsewhere on the board
/OPD/OPD_PWR: J1.15, J1.16; also elsewhere on the board
/OPD/OPD_SCL: J1.13, J1.14; also elsewhere on the board
/OPD/OPD_SDA: J1.11, J1.12; also elsewhere on the board
/OUT1_N: J2.5, J2.6; also elsewhere on the board
/OUT1_P: J2.7, J2.8; also elsewhere on the board
/SENSOR_ENABLE: J2.13, J2.14; also elsewhere on the board
/SPI_CLK: J2.17, J2.18; also elsewhere on the board
/SPI_MISO: J2.15, J2.16; also elsewhere on the board
/SPI_MOSI: J2.19, J2.20; also elsewhere on the board
/TXCLK_N: J2.1, J2.2; also elsewhere on the board
/TXCLK_P: J2.3, J2.4; also elsewhere on the board
/~SD: J1.39, J1.40
VBUS: J1.23, J1.24, J1.25, J1.26; also elsewhere on the board

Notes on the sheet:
Mechanical
Aux Connector
Fiducials (Front)
Future: route a "power is on" signal to the CFC Processor Card so it knows directly if the CFC Sensor Card is powered up or not.
Main OreSat Card Connector (Backplane v2)

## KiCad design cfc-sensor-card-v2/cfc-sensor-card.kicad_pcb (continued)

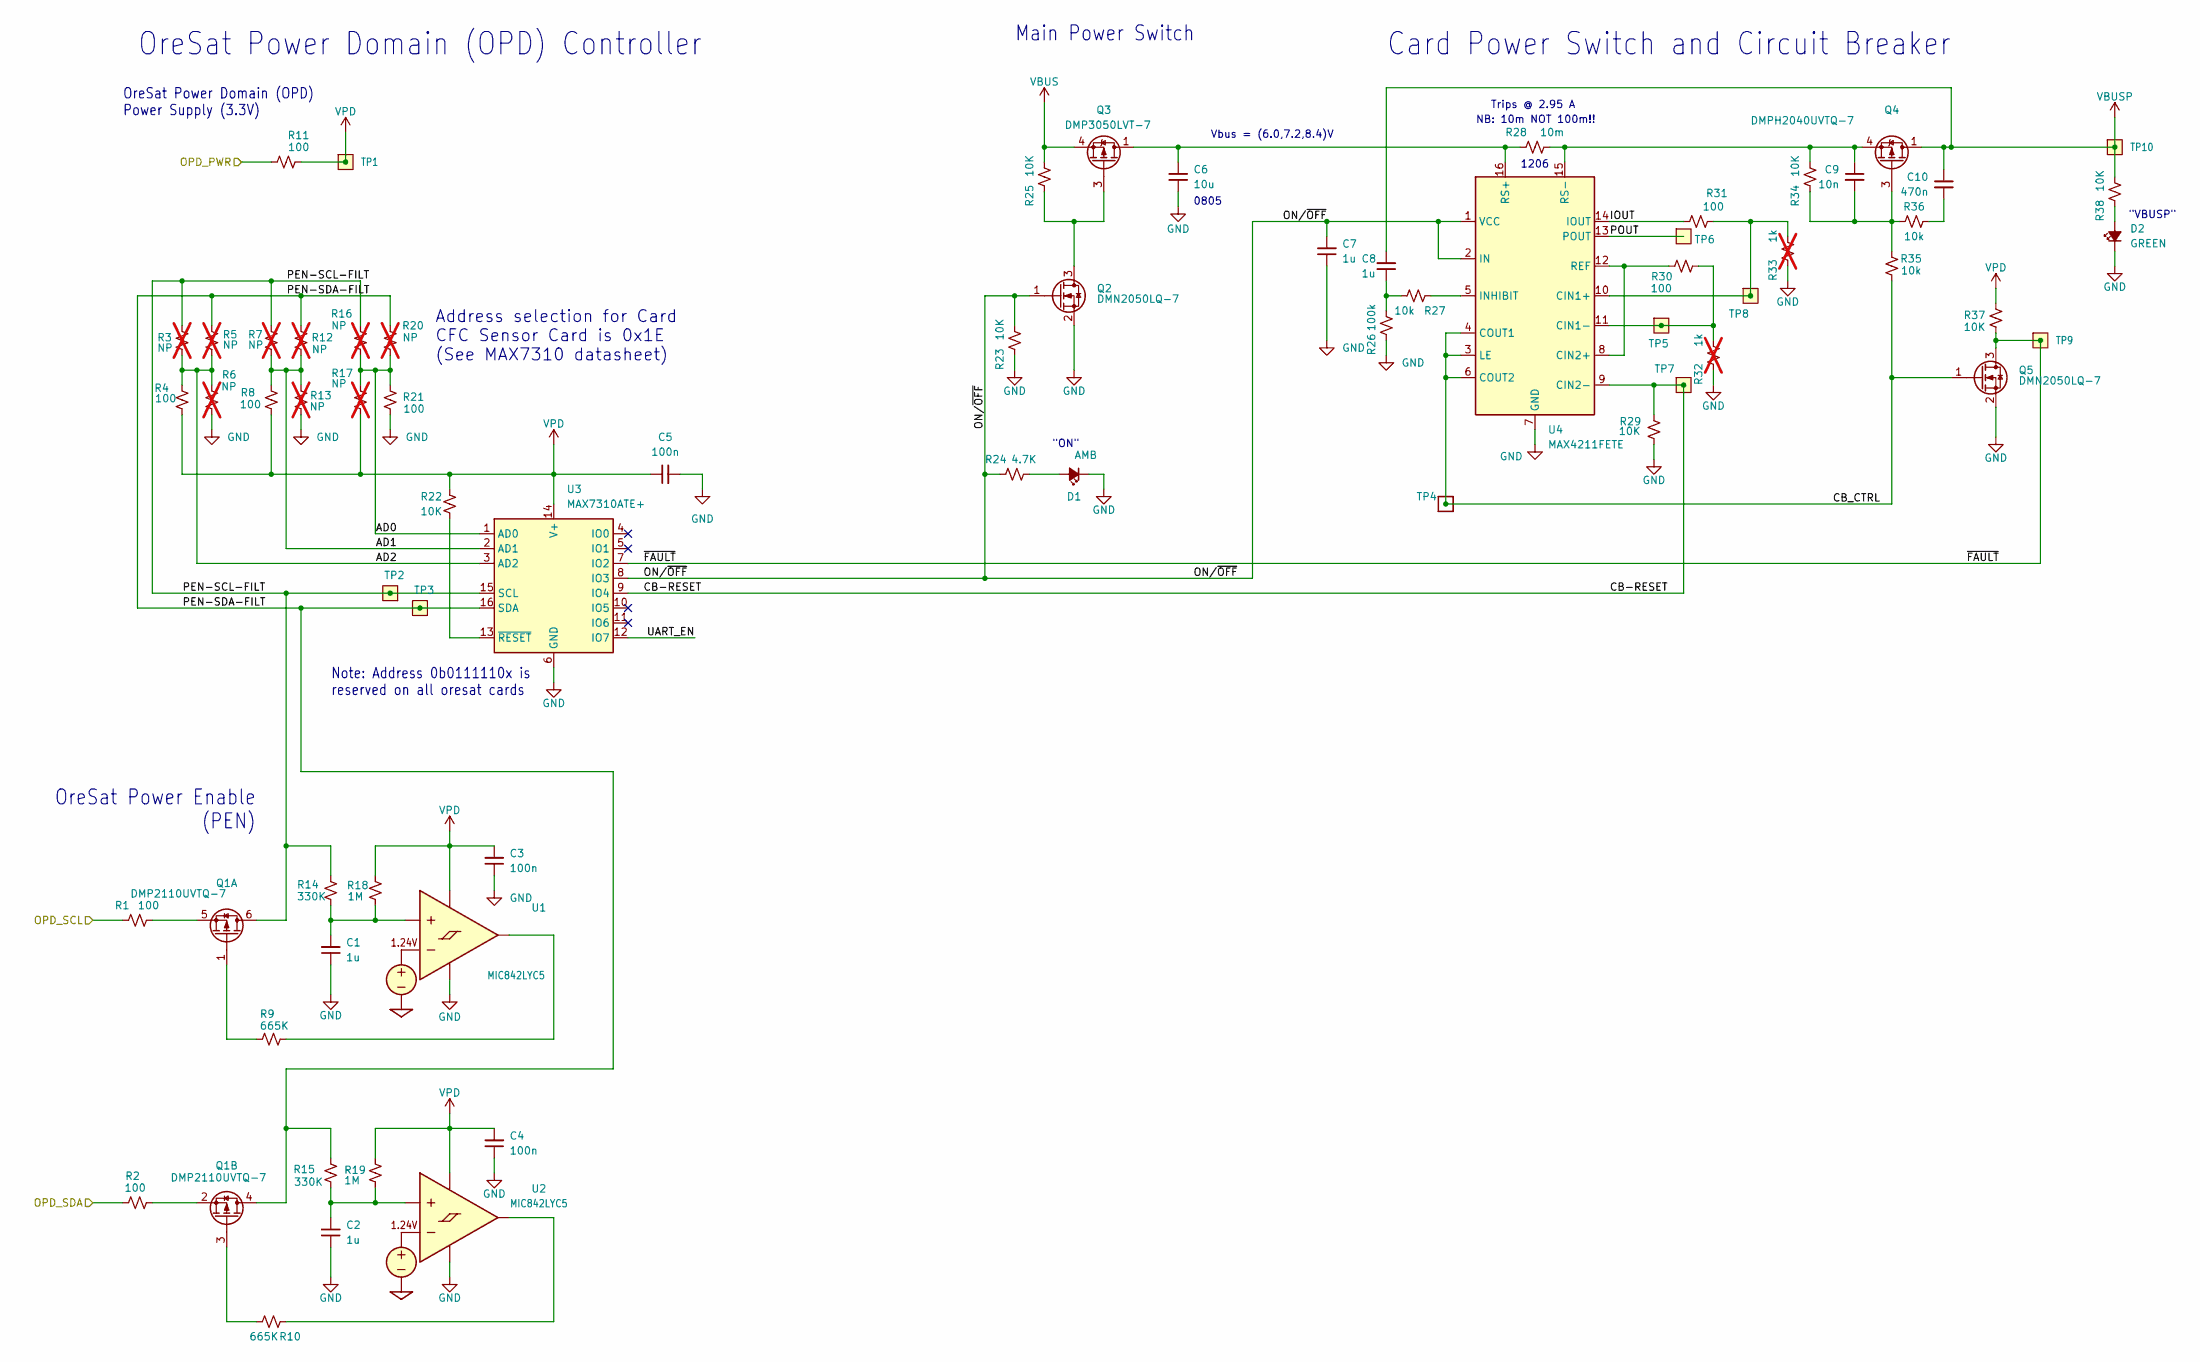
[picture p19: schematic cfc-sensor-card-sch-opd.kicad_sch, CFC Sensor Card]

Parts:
C1, C2, C7, C8: 1u; 0603-C-NOSILK; MPN TMK107BJ105KAHT
C3, C4, C5: 100n; 0603-C-NOSILK; MPN TMK107BJ104KAHT
C6: 10u; 0805-C-NOSILK; MPN GRT21BC71E106KE13L
C9: 10n; 0603-C-NOSILK; MPN C0603C103J5RACAUTO
C10: 470n; 0603-C-NOSILK; MPN C0603C474K3RACAUTO
D1: AMB; LED_0603_1608Metric; MPN 150060AS75000
D2: GREEN; LED_0603_1608Metric; MPN 150060GS75000
Q1: DMP2110UVTQ-7; SOT-23-6; MPN DMP2110UVTQ-7
Q2, Q5: DMN2050LQ-7; SOT-23; MPN DMN2050LQ-7
Q3: DMP3050LVT-7; TSOT-23-6; MPN DMP3050LVT-7
Q4: DMPH2040UVTQ-7; TSOT-23-6; MPN DMPH2040UVTQ-7
R1, R2, R4, R8, R11, R21, R30, R31: 100; 0603-C-NOSILK; MPN RMCF0603FT100R
R3, R5, R6, R7, R12, R13, R16, R17, R20: NP; 0603-C-NOSILK; not fitted
R9, R10: 665K; 0603-C-NOSILK; MPN RMCF0603FT665K
R14, R15: 330K; 0603-C-NOSILK; MPN RMCF0603FT330K
R18, R19: 1M; 0603-C-NOSILK; MPN RMCF0603FG1M00
R22, R23, R25, R29, R34, R37, R38: 10K; 0603-C-NOSILK; MPN RMCF0603FT10K0
R24: 4.7K; 0603-C-NOSILK; MPN RMCF0603FT4K70
R26: 100k; 0603-C-NOSILK; MPN RMCF0603FT100K
R27, R35, R36: 10k; 0603-C-NOSILK; MPN RMCF0603FT10K0
R28: 10m; R_1206_3216Metric; MPN CSRF1206FT10L0
R32, R33: 1k; 0603-C-NOSILK; not fitted
TP1, TP9, TP10: Test-Point; TestPoint-0.75mm-th
TP2, TP3, TP5, TP6, TP7, TP8: TEST-POINT; TestPoint-0.75mm-th
TP4: TestPoint-MinTH; TestPoint_Pad_D1.0mm
U1, U2: MIC842LYC5; SOT-353_SC-70-5; MPN MIC842LYC5-TR
U3: MAX7310ATE+; QFN-16-1EP_4x4mm_P0.65mm_EP2.1x2.1mm; MPN MAX7310ATE+
U4: MAX4211FETE; QFN-16-1EP_4x4mm_P0.65mm_EP2.1x2.1mm; MPN MAX4211FETE

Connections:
/OPD/AD0: R16.2, R17.1, R20.2, R21.1, U3.1 (AD0)
/OPD/AD1: R7.2, R8.1, R12.2, R13.1, U3.2 (AD1)
/OPD/AD2: R3.2, R4.1, R5.2, R6.1, U3.3 (AD2)
/OPD/CB-RESET: R29.2, TP7.1 (1_1), U3.9 (IO4), U4.9 (CIN2-)
/OPD/CB_CTRL: Q5.1 (G), R35.2, TP4.1 (1_1), U4.3 (LE), U4.4 (COUT1), U4.6 (COUT2)
/OPD/IOUT: R31.1, U4.14 (IOUT)
/OPD/ON/~OFF: C7.2, Q2.1 (G), R23.2, R24.1, U3.8 (IO3), U4.1 (VCC), U4.2 (IN)
/OPD/OPD_PWR: R11.1; also elsewhere on the board
/OPD/OPD_SCL: R1.1; also elsewhere on the board
/OPD/OPD_SDA: R2.1; also elsewhere on the board
/OPD/PEN-SCL-FILT: Q1.6 (D), R3.1, R7.1, R14.2, R16.1, TP2.1 (1_1), U3.15 (SCL)
/OPD/PEN-SDA-FILT: Q1.4 (D), R5.1, R12.1, R15.2, R20.1, TP3.1 (1_1), U3.16 (SDA)
/OPD/POUT: TP6.1 (1_1), U4.13 (POUT)
/OPD/UART_EN: U3.12 (IO7)
/OPD/~FAULT: Q5.3 (D), R37.1, TP9.1 (1_1), U3.7 (IO2)
unnamed: C8.1, R26.2, R27.2
unnamed: C10.2, R36.2
unnamed: D1.2 (A), R24.2
unnamed: D2.2 (A), R38.1
unnamed: Q1.1 (G), R9.2
unnamed: Q1.5 (S), R1.2
unnamed: Q1.3 (G), R10.2
unnamed: Q1.2 (S), R2.2
unnamed: Q2.3 (D), Q3.3 (G), R25.1
unnamed: C9.2, Q4.3 (G), R34.1, R35.1, R36.1
unnamed: C9.1, Q4.4 (S), R28.2, R34.2, U4.15 (RS-)
unnamed: C1.2, R14.1, R18.1, U1.1 (INP)
unnamed: R9.1, U1.4 (OUT)
unnamed: C2.2, R15.1, R19.1, U2.1 (INP)
unnamed: R10.1, U2.4 (OUT)
unnamed: R22.2, U3.13 (~RESET)
unnamed: R31.2, R33.2, TP8.1 (1_1), U4.10 (CIN1+)
unnamed: R30.2, R32.2, TP5.1 (1_1), U4.11 (CIN1-)
unnamed: R30.1, U4.8 (CIN2+), U4.12 (REF)
unnamed: R27.1, U4.5 (INHIBIT)
unnamed: C6.2, Q3.1 (D), Q3.2 (D), Q3.5 (D), Q3.6 (D), R28.1, U4.16 (RS+)
VBUS: Q3.4 (S), R25.2; also elsewhere on the board
VBUSP: C8.2, C10.1, Q4.1 (D), Q4.2 (D), Q4.5 (D), Q4.6 (D), R38.2, TP10.1 (1_1); also elsewhere on the board
VPD: C3.2, C4.2, C5.1, R4.2, R8.2, R11.2, R17.2, R18.2, R19.2, R22.1, R37.2, TP1.1 (1_1), U1.5 (VDD), U2.5 (VDD), U3.14 (V+)

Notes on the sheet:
Trips @ 2.95 A
Vbus = (6.0,7.2,8.4)V
1206
OreSat Power Domain (OPD) Power Supply (3.3V)
NB: 10m NOT 100m!!
OreSat Power Domain (OPD) Controller
Card Power Switch and Circuit Breaker
Note: Address 0b0111110x is reserved on all oresat cards
"ON"
Address selection for Card CFC Sensor Card is 0x1E (See MAX7310 datasheet)
0805
OreSat Power Enable (PEN)
Main Power Switch
"VBUSP"

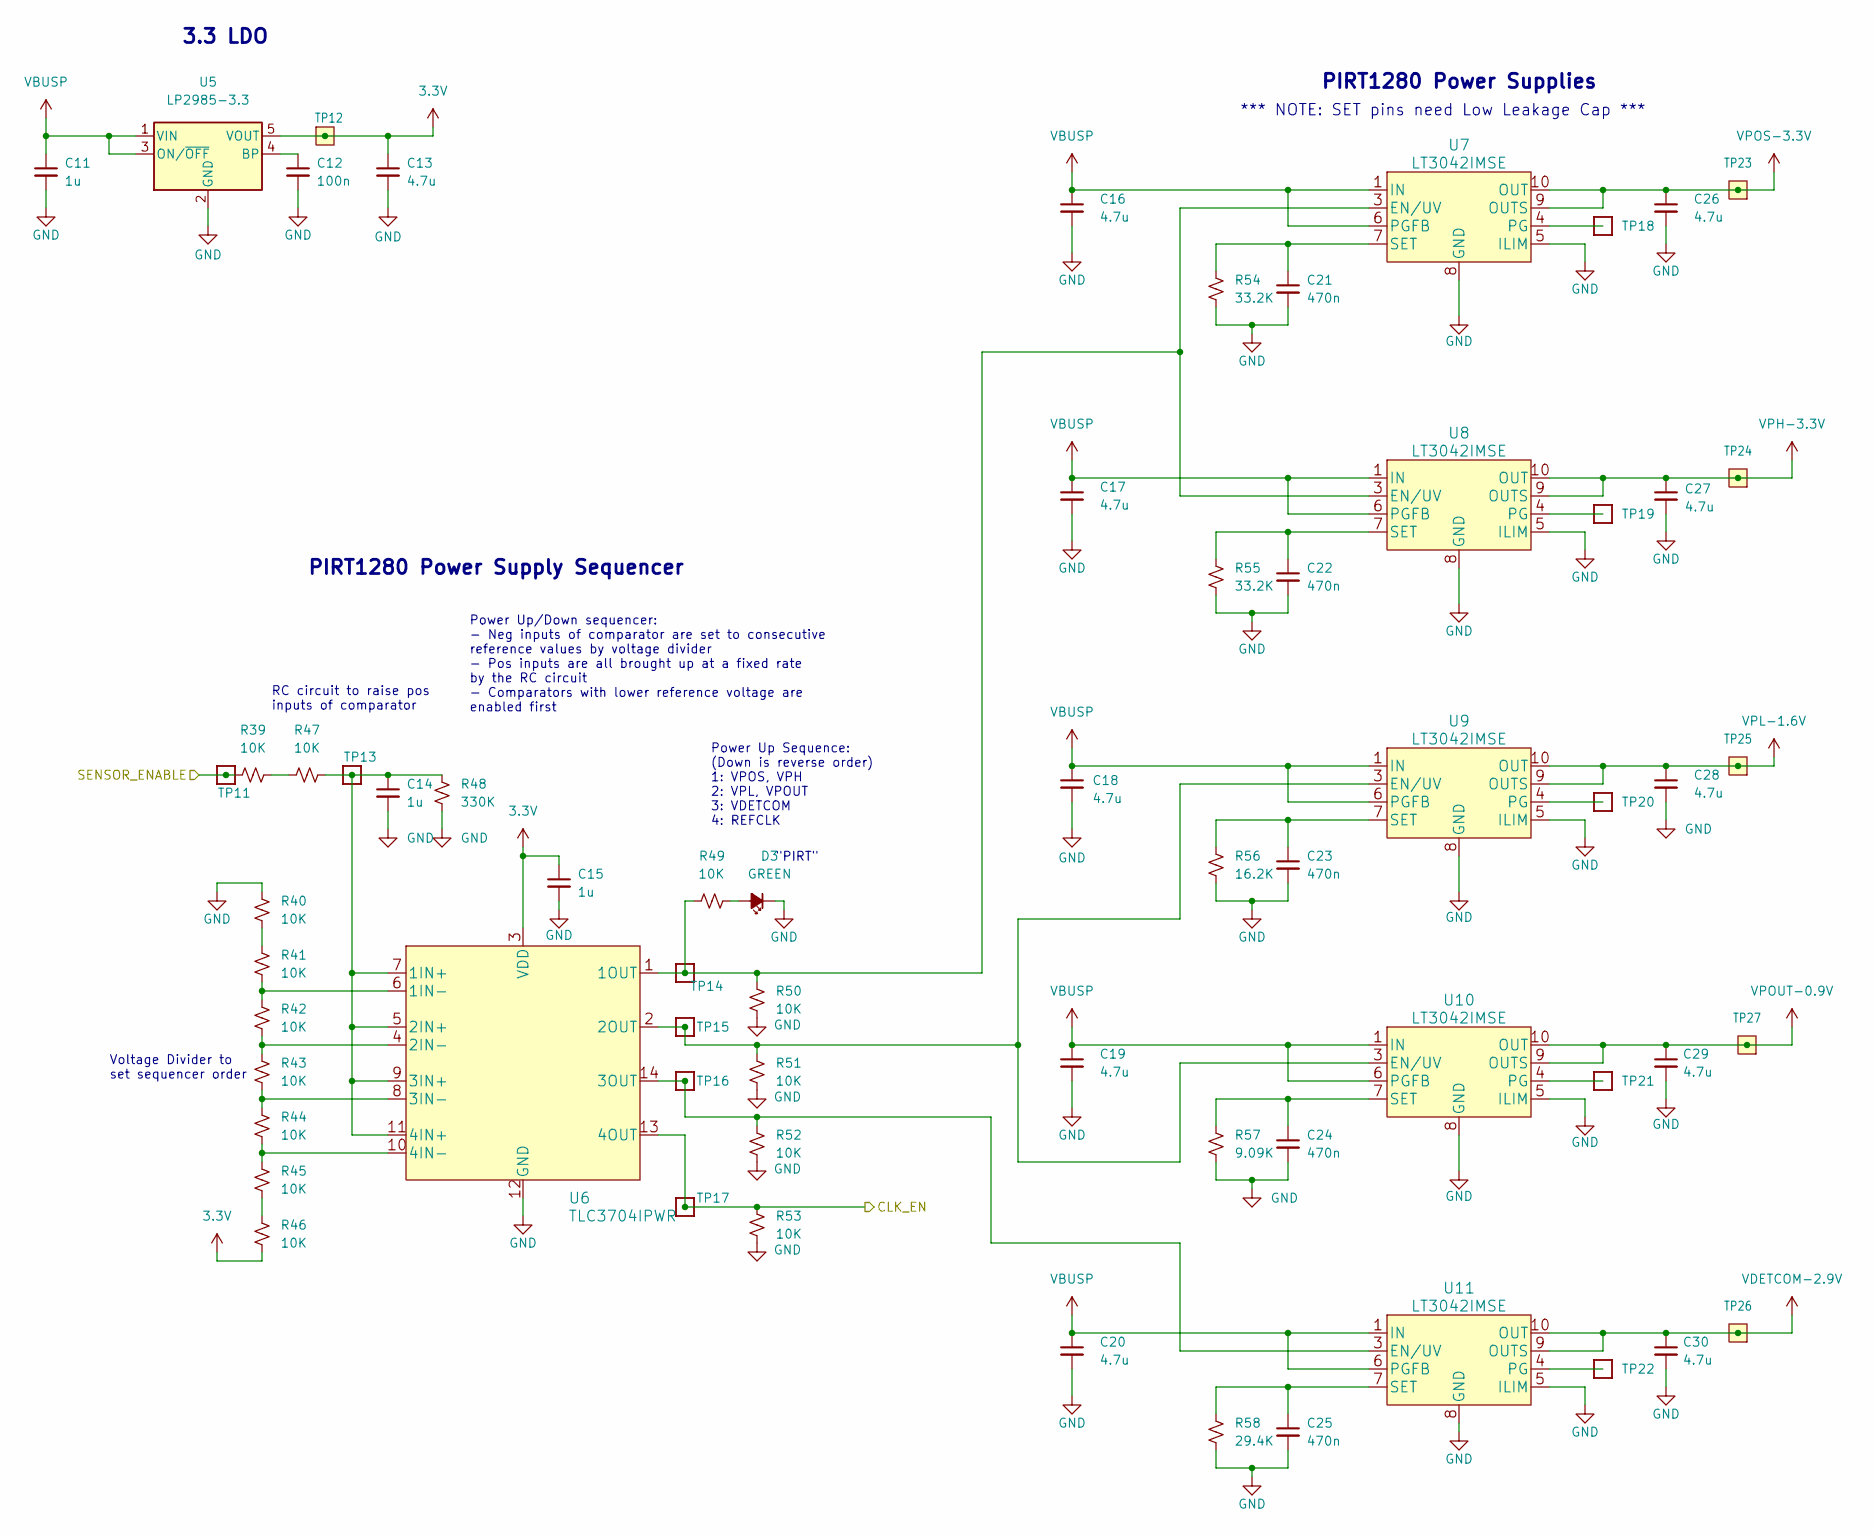
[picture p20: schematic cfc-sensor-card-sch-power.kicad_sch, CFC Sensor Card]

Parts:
C11, C14, C15: 1u; 0603-C-NOSILK; MPN TMK107BJ105KAHT
C12: 100n; 0603-C-NOSILK; MPN TMK107BJ104KAHT
C13, C16, C17, C18, C19, C20, C26, C27, C28, C29, C30: 4.7u; 0603-C-NOSILK; MPN EMK107BBJ475KAHT
C21, C22, C23, C24, C25: 470n; 0603-C-NOSILK; MPN C0603C474K3RACAUTO
D3: GREEN; LED_0603_1608Metric; MPN 150060GS75000
R39, R40, R41, R42, R43, R44, R45, R46, R47, R49, R50, R51, R52, R53: 10K; 0603-C-NOSILK; MPN RMCF0603FT10K0
R48: 330K; 0603-C-NOSILK; MPN RMCF0603FT330K
R54, R55: 33.2K; 0603-C-NOSILK; MPN RMCF0603FT33K2
R56: 16.2K; 0603-C-NOSILK; MPN RMCF0603FT16K2
R57: 9.09K; 0603-C-NOSILK; MPN RMCF0603FT9K09
R58: 29.4K; 0603-C-NOSILK; MPN RMCF0603FT29K4
TP11, TP13, TP14, TP15, TP16, TP17, TP18, TP19, TP20, TP21, TP22: TestPoint-MinTH; TestPoint_Pad_D1.0mm
TP12, TP23, TP24, TP25, TP26, TP27: Test-Point; TestPoint-0.75mm-th
U5: LP2985-3.3; SOT-23-5; MPN LP2985AIM5-3.3/NOPB
U6: TLC3704IPWR; TSSOP-14_4.4x5mm_P0.65mm; MPN TLC3704IPWR
U7, U8, U9, U10, U11: LT3042IMSE; MSOP-10-1EP_3x3mm_P0.5mm_EP1.68x1.88mm_0.254_ThermalVias; MPN LT3042IMSE#TRPBF

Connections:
3.3V: C13.1, C15.1, R46.2, TP12.1 (1_1), U5.5 (VOUT), U6.3 (VDD); also elsewhere on the board
/PIRT/CLK_EN: R53.1, TP17.1 (1_1), U6.13 (4OUT); also elsewhere on the board
/SENSOR_ENABLE: R39.1, TP11.1 (1_1); also elsewhere on the board
unnamed: D3.2 (A), R49.2
unnamed: R39.2, R47.1
unnamed: R40.2, R41.1
unnamed: R45.2, R46.1
unnamed: C12.1, U5.4 (BP)
unnamed: C14.1, R47.2, R48.2, TP13.1 (1_1), U6.5 (2IN+), U6.7 (1IN+), U6.9 (3IN+), U6.11 (4IN+)
unnamed: R41.2, R42.1, U6.6 (1IN-)
unnamed: R49.1, R50.1, TP14.1 (1_1), U6.1 (1OUT), U7.3 (EN/UV), U8.3 (EN/UV)
unnamed: R42.2, R43.1, U6.4 (2IN-)
unnamed: R43.2, R44.1, U6.8 (3IN-)
unnamed: R44.2, R45.1, U6.10 (4IN-)
unnamed: TP18.1 (1_1), U7.4 (PG)
unnamed: C21.1, R54.1, U7.7 (SET)
unnamed: TP19.1 (1_1), U8.4 (PG)
unnamed: C22.1, R55.1, U8.7 (SET)
unnamed: TP20.1 (1_1), U9.4 (PG)
unnamed: C23.1, R56.1, U9.7 (SET)
unnamed: R51.1, TP15.1 (1_1), U6.2 (2OUT), U9.3 (EN/UV), U10.3 (EN/UV)
unnamed: TP21.1 (1_1), U10.4 (PG)
unnamed: C24.1, R57.1, U10.7 (SET)
unnamed: R52.1, TP16.1 (1_1), U6.14 (3OUT), U11.3 (EN/UV)
unnamed: TP22.1 (1_1), U11.4 (PG)
unnamed: C25.1, R58.1, U11.7 (SET)
VBUSP: C11.1, C16.1, C17.1, C18.1, C19.1, C20.1, U5.1 (VIN), U5.3 (ON/~OFF), U7.1 (IN), U7.2 (IN), U7.6 (PGFB), U8.1 (IN), U8.2 (IN), U8.6 (PGFB), U9.1 (IN), U9.2 (IN), U9.6 (PGFB), U10.1 (IN), U10.2 (IN), U10.6 (PGFB), U11.1 (IN), U11.2 (IN), U11.6 (PGFB); also elsewhere on the board
VDETCOM-2.9V: C30.1, TP26.1 (1_1), U11.9 (OUTS), U11.10 (OUT); also elsewhere on the board
VPH-3.3V: C27.1, TP24.1 (1_1), U8.9 (OUTS), U8.10 (OUT); also elsewhere on the board
VPL-1.6V: C28.1, TP25.1 (1_1), U9.9 (OUTS), U9.10 (OUT); also elsewhere on the board
VPOS-3.3V: C26.1, TP23.1 (1_1), U7.9 (OUTS), U7.10 (OUT); also elsewhere on the board
VPOUT-0.9V: C29.1, TP27.1 (1_1), U10.9 (OUTS), U10.10 (OUT); also elsewhere on the board

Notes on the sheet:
RC circuit to raise pos inputs of comparator
Voltage Divider to set sequencer order
Power Up/Down sequencer: - Neg inputs of comparator are set to consecutive reference values by voltage divider - Pos inputs are all brought up at a fixed rate by the RC circuit - Comparators with lower reference voltage are enabled first
PIRT1280 Power Supply Sequencer
"PIRT"
*** NOTE: SET pins need Low Leakage Cap ***
Power Up Sequence: (Down is reverse order) 1:  VPOS, VPH 2: VPL, VPOUT 3: VDETCOM 4: REFCLK
3.3 LDO
PIRT1280 Power Supplies


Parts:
C31, C32, C33, C34, C35, C39, C41, C42: 100n; 0603-C-NOSILK; MPN TMK107BJ104KAHT
C36, C38, C40: 10u; 0805-C-NOSILK; MPN GRT21BC71E106KE13L
C37: 10n; 0603-C-NOSILK; MPN KGM15AR71H103KT
C43: .022uF; 0603-C-NOSILK; MPN KAM15AR71H223JT
D4, D6: GREEN; LED_0603_1608Metric; MPN 150060GS75000
D5: AMBER; LED_0603_1608Metric; MPN 150060AS75000
L1: 2.6u; Ind 2.6u 2A; MPN SRR5028-2R6Y
R59, R60, R67: 10K; 0603-C-NOSILK; MPN RMCF0603FT10K0
R61, R66: 10K; 0603-C-NOSILK; MPN RNCF0603TKW10K0
R62: 4.7K; 0603-C-NOSILK; MPN RMCF0603FT4K70
R63: 1k; 0603-C-NOSILK; MPN RMCF0603FT1K00
R64: 50m; 1206-C; MPN KDV12DR050ET
R65: 18K; 0603-C-NOSILK; MPN TNPW060318K0BYCN
R68: 1.4K; 0603-C-NOSILK; MPN RQ73C1J1K4BTD
R69, R70: 100; 0603-C-NOSILK; MPN RMCF0603FT100R
R71: 25m; R_2512_6332Metric; MPN CSNL2512FT25L0
U12: AD5593RBCPZ-RL7; 16-WFQFN, CSP; MPN AD5593RBCPZ-RL7
U13: SN74LVC1G86DBVR; DBV5; MPN SN74LVC1G86DBVR
U14: SN74LVC1G08DCKR; DCK5-L; MPN SN74LVC1G08DCKR
U15: MP2410A; TSOT-23-6; MPN MP2410AGJ-Z
U16: DRV8212DSGR; WSON_212DSGR_TEX; MPN DRV8212DSGR
U17: INA186A1IDCKR; SOIC_IDCKR_TEX; MPN INA186A1IDCKR

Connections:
2.5VREF: C31.1, R61.1, R66.1, U12.6 (VREF)
3.3V: C32.1, C33.1, C35.1, C39.1, C42.1, R59.1, U12.1 (VDD), U12.7 (VLOGIC), U12.15 (~RESET), U13.5 (VCC), U14.5 (VCC), U16.7 (MODE), U16.8 (VCC), U17.3 (VS); also elsewhere on the board
/I2C1_CLK: U12.14 (SCL); also elsewhere on the board
/I2C1_SDA: U12.13 (SDA); also elsewhere on the board
/PIRT/THERM+: C34.1, R61.2, U12.11 (I/O7); also elsewhere on the board
/TEC Control/BRIDGE_DIR: U12.4 (I/O2), U13.2 (B), U14.2 (B), U16.6 (IN1/PH)
/TEC Control/BRIDGE_EN: U12.3 (I/O1), U13.1 (A), U14.1 (A), U16.5 (IN2/EN)
/TEC Control/CURRENT_SET: U12.2 (I/O0), U15.5 (EN/DIM)
/TEC Control/TEC_SENSE: U12.5 (I/O3), U17.6 (OUT)
unnamed: C38.2, R63.2, R64.1
unnamed: D4.2 (A), R60.1
unnamed: D5.2 (A), R62.2
unnamed: D6.2 (A), R67.1
unnamed: R59.2, U12.16 (A0)
unnamed: C37.1, U15.6 (BST)
unnamed: R63.1, U15.4 (FB)
unnamed: C37.2, L1.1, U15.2 (SW)
unnamed: R69.2, R71.1, U16.3 (OUT2)
unnamed: C38.1, C40.1, C41.1, L1.2, R67.2, U16.1 (VM)
unnamed: C43.1, R69.1, U17.4 (IN+)
unnamed: C43.2, R70.1, U17.5 (IN-)
unnamed: R65.1, R66.2, R68.1, U17.1 (REF)
VBUSP: C36.1, U15.3 (VIN); also elsewhere on the board

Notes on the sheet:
0805
2A max
1.649v voltage divider
VM max = 11volts VM min = 1.65volts
XOR Gate
PIRT1280 Thermistor
.0495*25=1.2375v .0505v*25=1.2625v
Scale voltage between .7-1.44v for 0-2A CC output
25v/v gain
TEC res= 2.8ohms 2a output = V/2.8 V=5.6
Constant Current Buck SPS
Bulk cap may need to change depending on output current
"COOL"
"TEC"
"HEAT"
10k resistor is upper resistor of divider and the PIRT1280 10k thermistor is the lower resistor
2512
Max 2a output V=2*.025±1% =.0495-.0505v .0505v*2a =.191watts
AND Gate


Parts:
C44, C45, C46, C47, C48, C49: 100n; 0603-C-NOSILK; MPN TMK107BJ104KAHT
TP28, TP29: TestPoint-MinTH; TestPoint_Pad_D1.0mm
U18: XO_ISM95-XXXXXX; MPN ISM95-3251AH-16.000MHZ
U19: U-PIRT-PIRT1280A1-12; PIRT1280A1-12; MPN PIRT1280A1-12

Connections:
3.3V: C44.1, U18.4 (VCC); also elsewhere on the board
/OUT1_N: U19.14 (OUT1N); also elsewhere on the board
/OUT1_P: U19.13 (OUT1P); also elsewhere on the board
/PIRT/CLK_EN: U18.1 (INH); also elsewhere on the board
/PIRT/THERM+: U19.1 (THERM+); also elsewhere on the board
/SPI_CLK: U19.26 (SDCLK); also elsewhere on the board
/SPI_MISO: U19.27 (SDOUT); also elsewhere on the board
/SPI_MOSI: U19.25 (SDIN); also elsewhere on the board
/TXCLK_N: U19.16 (TXCLKN); also elsewhere on the board
/TXCLK_P: U19.15 (TXCLKP); also elsewhere on the board
unnamed: TP28.1 (1_1), U18.3 (CLK), U19.20 (REFCLK)
unnamed: TP29.1 (1_1), U19.21 (JAMSYNC)
VDETCOM-2.9V: C47.1, U19.31 (VDETCOM-2.9V); also elsewhere on the board
VPH-3.3V: C48.1, U19.19 (VPH-3.3V); also elsewhere on the board
VPL-1.6V: C46.1, U19.18 (VPL-1.6V); also elsewhere on the board
VPOS-3.3V: C49.1, U19.30 (VPOS-3.3V); also elsewhere on the board
VPOUT-0.9V: C45.1, U19.5 (VPOUT-0.9V); also elsewhere on the board

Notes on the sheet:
PIRT1280 16MHz Oscillator
PIRT1208 Detector

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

Board: 4 copper layers, 99.8 x 94.6 mm, 182 parts (1 on the bottom side), 107 nets.

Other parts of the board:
PCB1: ORESAT-CARD-V1.3-CFC-SENSOR-V1.0

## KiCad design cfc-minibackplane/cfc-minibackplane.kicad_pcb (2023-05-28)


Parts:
C1, C2, C3, C4: 10u 25V; C_1206_3216Metric; MPN 490-14533-1-ND
C1.1, C1.2, C3.1, C3.2: 1n; C_0603_1608Metric; MPN GCM1885C2A102JA16D
CF1.1, CF2.1, CF3.1: SFM-110-X1-XXX-D-LC; J-SAMTEC-CF-SFM-110-X1-XXX-D-LC; MPN SFM-110-01-L-D-LC
CF1.2, CF2.2, CF3.2: SFM-120-X1-XXX-D; J-SAMTEC-SFM-120-X1-XXX-D; MPN SFM-120-01-L-D-LC
J1: m55-6001642; MPN 952-3836-1-ND
J2: Harwin M80-5100442; J-Harwin-M80-5100442; MPN M80-5100442
J3: PC 180926; PhoenixContact_MSTBV_2,5_2-GF_1x02_P5.00mm_Vertical_Threade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; MPN 1809267
J3.1: PC 1861690; MPN 1861690
J4: ORESAT-DEBUG-CONNECTOR-ALL; J-TE_2-1734592-0_FFC_MIRRORED; MPN 2-1734592-0
R1: 100k; R_0603_1608Metric; MPN ESR18EZPF1003
R1.1, R1.2, R1.3, R1.4, R3.1, R3.2, R3.3, R3.4: 60.4; R_1206_3216Metric; MPN ESR18EZPF60R4
R2, R3: 4k7; R_0603_1608Metric; MPN RMCF0603FT4K70
R4, R5: 0; R_0603_1608Metric; MPN RMCF0603ZT0R00
U1: Trinket M0; Adafruit-Trinket; MPN 3500
U2: AMS1117-3.3; SOT-223-3_TabPin2; MPN AMS1117-3.3

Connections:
AUX-1: CF1.1.1, CF1.1.2, CF2.1.1, CF2.1.2, CF3.1.1, CF3.1.2
AUX-2: CF1.1.3, CF1.1.4, CF2.1.3, CF2.1.4, CF3.1.3, CF3.1.4
AUX-3: CF1.1.5, CF1.1.6, CF2.1.5, CF2.1.6, CF3.1.5, CF3.1.6
AUX-4: CF1.1.7, CF1.1.8, CF2.1.7, CF2.1.8, CF3.1.7, CF3.1.8
AUX-5: CF1.1.9, CF1.1.10, CF2.1.9, CF2.1.10, CF3.1.9, CF3.1.10
AUX-6: CF1.1.11, CF1.1.12, CF2.1.11, CF2.1.12, CF3.1.11, CF3.1.12
AUX-7: CF1.1.13, CF1.1.14, CF2.1.13, CF2.1.14, CF3.1.13, CF3.1.14
AUX-8: CF1.1.15, CF1.1.16, CF2.1.15, CF2.1.16, CF3.1.15, CF3.1.16
AUX-9: CF1.1.17, CF1.1.18, CF2.1.17, CF2.1.18, CF3.1.17, CF3.1.18
AUX-10: CF1.1.19, CF1.1.20, CF2.1.19, CF2.1.20, CF3.1.19, CF3.1.20
C3-UART-RX: CF1.2.38, CF2.2.38, CF3.2.38, J1.b8
C3-UART-TX: CF1.2.37, CF2.2.37, CF3.2.37, J1.a7
CAN1_H: CF1.2.33, CF1.2.34, CF2.2.33, CF2.2.34, CF3.2.33, CF3.2.34, J1.a6, R1.3.2, R3.3.1, R4.1
CAN1_L: CF1.2.35, CF1.2.36, CF2.2.35, CF2.2.36, CF3.2.35, CF3.2.36, J1.b7, R1.4.1, R3.4.2, R5.1
CAN2_H: CF1.2.17, CF1.2.18, CF2.2.17, CF2.2.18, CF3.2.17, CF3.2.18, J1.a2, R1.1.2, R3.1.1, R4.2
CAN2_L: CF1.2.19, CF1.2.20, CF2.2.19, CF2.2.20, CF3.2.19, CF3.2.20, J1.b3, R1.2.1, R3.2.2, R5.2
EEPROM_WP: J4.20 (DEBUG-3)
GND: C1.2, C1.1.2, C1.2.2, C2.2, C3.2, C3.1.2, C3.2.2, C4.2, CF1.1.LC1, CF1.1.LC2, CF1.2.27, CF1.2.28, CF1.2.29, CF1.2.30, CF1.2.31, CF1.2.32, CF1.2.LC1, CF1.2.LC2, CF2.1.LC1, CF2.1.LC2, CF2.2.27, CF2.2.28, CF2.2.29, CF2.2.30, CF2.2.31, CF2.2.32, CF2.2.LC1, CF2.2.LC2, CF3.1.LC1, CF3.1.LC2, CF3.2.27, CF3.2.28, CF3.2.29, CF3.2.30, CF3.2.31, CF3.2.32, CF3.2.LC1, CF3.2.LC2, J1.b4, J1.b5, J1.b6, J1.mech, J2.3, J3.2, J4.3 (GND), J4.6 (GND), J4.9 (GND), J4.PAD1 (PAD), J4.PAD2 (PAD), U1.2 (GND), U2.1 (GND)
HELICAL-DEPLOY: CF1.2.7, CF1.2.8, CF2.2.7, CF2.2.8, CF3.2.7, CF3.2.8
I2C0_SCL: J4.18 (DEBUG-1)
I2C0_SDA: J4.19 (DEBUG-2)
MAG-POWER: CF1.2.5, CF1.2.6, CF2.2.5, CF2.2.6, CF3.2.5, CF3.2.6
MAG-SCL: CF1.2.3, CF1.2.4, CF2.2.3, CF2.2.4, CF3.2.3, CF3.2.4
MAG-SDA: CF1.2.1, CF1.2.2, CF2.2.1, CF2.2.2, CF3.2.1, CF3.2.2
unnamed: C1.1.1, R1.1.1, R1.2.2
unnamed: C1.2.1, R1.3.1, R1.4.2
unnamed: C3.1.1, R3.1.2, R3.2.1
unnamed: C3.2.1, R3.3.2, R3.4.1
unnamed: J2.1, R1.2
OPD_PWR: C4.1, CF1.2.15, CF1.2.16, CF2.2.15, CF2.2.16, CF3.2.15, CF3.2.16, J1.b2, R2.1, R3.1, U1.6 (3v), U2.2 (VO)
OPD_SCL: CF1.2.13, CF1.2.14, CF2.2.13, CF2.2.14, CF3.2.13, CF3.2.14, J1.a1, R3.2, U1.8 (GPIO1)
OPD_SDA: CF1.2.11, CF1.2.12, CF2.2.11, CF2.2.12, CF3.2.11, CF3.2.12, J1.b1, R2.2, U1.9 (GPIO0)
TURNSTILE-DEPLOY: CF1.2.9, CF1.2.10, CF2.2.9, CF2.2.10, CF3.2.9, CF3.2.10
UART0_RX: J4.12 (CARD-RX)
UART0_TX: J4.13 (CARD-TX)
USB_CLI_N: J2.2, J4.5 (DEVICE-D-)
USB_CLI_P: J2.4, J4.4 (DEVICE-D+)
USB_CLI_VBUS: J4.1 (VBUSP), J4.2 (VBUSP), R1.1
VBUS: C1.1, C2.1, C3.1, CF1.2.21, CF1.2.22, CF1.2.23, CF1.2.24, CF1.2.25, CF1.2.26, CF2.2.21, CF2.2.22, CF2.2.23, CF2.2.24, CF2.2.25, CF2.2.26, CF3.2.21, CF3.2.22, CF3.2.23, CF3.2.24, CF3.2.25, CF3.2.26, J1.a3, J1.a4, J1.a5, J3.1, U2.3 (VI)
~SD: CF1.2.39, CF1.2.40, CF2.2.39, CF2.2.40, CF3.2.39, CF3.2.40, J1.a8

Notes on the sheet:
To Card Under Test via 20 cond. FFC
OPD_PWR
Ext Debug Connector
C3 UART
CAN2
OPD Control
Can Bridge
Use R4, R5 to bridge CAN1 and CAN2
Vbus
Ext USB
CAN1
OPD I2C
USB Debug Connector
CLI USB
THIS DEBUG BOARD REQUIRES MIRRORED FFC CONNECTOR
Power
Main Connectors
Power Plug
Aux connectors



Board: 2 copper layers, 116.8 x 31.3 mm, 33 parts (18 on the bottom side), 35 nets.

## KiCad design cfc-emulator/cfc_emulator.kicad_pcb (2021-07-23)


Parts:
C1, C4, C14, C17, C19: C0805C104Z5VACTU; C_0805_2012Metric_Pad1.18x1.45mm_HandSolder
C2: C0805C104Z5VACTU; C_0402_1005Metric_Pad0.74x0.62mm_HandSolder
C3, C5, C7, C12, C15: C0603C103M5RACTU; C_0603_1608Metric_Pad1.08x0.95mm_HandSolder
C6, C8, C9, C11, C13, C16: GRM155R71H102KA01J; C_0402_1005Metric_Pad0.74x0.62mm_HandSolder
C10: GRM188R61A106KE69J; C_0603_1608Metric_Pad1.08x0.95mm_HandSolder
C18: C0603C103M5RACTU; C_0402_1005Metric_Pad0.74x0.62mm_HandSolder
J1: pirt_test_conn
J2: PMOD1A; PMOD
J3: PMOD1B; PMOD
U1: DS90CR217MTD_NOPBMTD48_TEX-L; MTD48

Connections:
+3V3: C1.1, C2.1, C3.1, C4.1, C5.1, C6.1, C7.1, C8.1, C9.1, C10.1, C11.1, C12.1, C13.1, C14.1, C15.1, C16.1, C17.1, C18.1, C19.1, J1.19 (VPH-3.3V), U1.2 (VCC_2), U1.8 (VCC_3), U1.14 (VCC_4), U1.21 (VCC), U1.30 (PLL_VCC), U1.37 (LVDS_VCC)
/LVDS0+: J1.14 (OUT1N), U1.40 (TXOUT0+)
/LVDS0-: J1.13 (OUT1P), U1.41 (TXOUT0-)
/LVDS1+: U1.38 (TXOUT1+)
/LVDS1-: U1.39 (TXOUT1-)
/LVDS2+: U1.34 (TXOUT2+)
/LVDS2-: U1.35 (TXOUT2-)
/LVDSCLK+: J1.16 (TXCLKN), U1.32 (TXCLK_OUT+)
/LVDSCLK-: J1.15 (TXCLKP), U1.33 (TXCLK_OUT-)
/SDCLK: J1.26 (SDCLK), J3.10
/SDIN: J1.25 (SDIN), J3.9
/SDOUT: J1.27 (SDOUT), J3.8
/TXCLK: J3.1, U1.26 (TXCLK_IN)
/TXIN0: J2.1, U1.44 (TXIN0)
/TXIN1: J2.2, U1.45 (TXIN1)
/TXIN2: J2.3, U1.47 (TXIN2)
/TXIN3: J2.4, U1.48 (TXIN3)
/TXIN4: J2.7, U1.1 (TXIN4)
/TXIN5: J2.8, U1.3 (TXIN5)
/TXIN6: J2.9, U1.4 (TXIN6)
/TXIN7: J2.10, U1.6 (TXIN7)
GND: C1.2, C2.2, C3.2, C4.2, C5.2, C6.2, C7.2, C8.2, C9.2, C10.2, C11.2, C12.2, C13.2, C14.2, C15.2, C16.2, C17.2, C18.2, C19.2, J1.29 (VGND), J2.5, J2.11, J3.5, J3.11, U1.11 (GND)


Board: 2 copper layers, 51.3 x 51.1 mm, 23 parts (0 on the bottom side), 18 nets.

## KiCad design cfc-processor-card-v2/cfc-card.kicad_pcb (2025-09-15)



Board: 4 copper layers, 99.8 x 94.6 mm, 250 parts (33 on the bottom side), 193 nets.

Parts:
C1, C7, C16, C17, C20, C28: 1n; 0402-C-NOSILK
C2, C8, C38, C44, C49: 10u; 0805-C-NOSILK
C3, C5, C6, C9, C10, C12, C32, C33, C34, C35, C37: 1u; 0603-C-NOSILK
C4, C11, C15, C18, C31, C39, C41, C50, C51: 100n; 0603-C-NOSILK
C13, C14, C36, C40: 22u; C_1210_3225Metric
C19, C22: 10p; 0603-C-NOSILK
C21, C23, C24, C25, C26, C27: 10n; 0402-C-NOSILK
C29, C30: 18p; 0603-C-NOSILK
C42, C43, C45, C46, C47, C48: 100n; 0402-C-NOSILK
D1, D7, D8: GREEN; LED_0603_1608Metric
D2, D3, D4, D5: BLUE; LED_0603_1608Metric
D6: AMBER; LED_0603_1608Metric
FB1: BLM18KG300JH1D; L_0603_1608Metric
FID1, FID2, FID3, FID4, FID5, FID6: Fiducial; Fiducial_1mm_Mask2mm
J1: 2-1734592-0; J-TE-2-1734592-0
J2: J-SAMTEC-TFM-110-X1-XXX-D-RA
J3: Conn_01x02; PinHeader_1x02_P2.54mm_Vertical
J4: TFM-120-01-L-D-RA; J-SAMTEC-TFM-120-X1-XXX-D-RA
J5: Conn_01x04; PinHeader_1x04_P2.54mm_Vertical
J6: DM3BT-DSF-PEJS; J-Hirose-DM3BT-DSF-PEJS
JP1: JUMPER-SMT_2_NC_TRACE_SILK; SMT-JUMPER_2_NC_TRACE_SILK
L1: 6.8u; L_ECS-MPI4040
PCB1: ORESAT-CARD-V1.3-GENERIC-0RF
Q1: MMBT2907; SOT-23
Q2, Q4: PMV45EN; SOT-23-3
Q3: DMP2240UDM; SOT-23-6
Q5, Q6: DMP3050LVT-7; TSOT-23-6
R1, R2, R3, R4, R5, R53, R54, R55, R56, R57, R58, R65, R66, R67, R68, R69, R70: 1k; 0603-C-NOSILK
R6, R7, R29, R30: 100; 0402-C-NOSILK
R11, R12, R15, R20, R21, R22, R24, R25, R26, R28, R32, R38, R39, R42, R46, R50, R52, R64, R72: 10k; 0603-C-NOSILK
R13, R27, R36, R44: 1M; 0603-C-NOSILK
R18, R19, R41, R48, R71: 100; 0603-C-NOSILK
R23: 499; 0603-C-NOSILK
R31: 40.2K; 0603-C-NOSILK
R33: 100k; 0603-C-NOSILK
R35, R43: 665k; 0603-C-NOSILK
R37, R45: 330k; 0603-C-NOSILK
R47: 0; 0603-C-NOSILK
R49, R61, R62: 2.7k; 0603-C-NOSILK
R51: 4.7k; 0603-C-NOSILK
R63: 100m; 1206-C
RA1, RA2, RA3: 10K; ARRAY_EXBA-M
RA4, RA5: 47k; RES_EXB2HV
TP1, TP2, TP18, TP19, TP20, TP21, TP23, TP24, TP26, TP27, TP28, TP29, TP30, TP31, TP32, TP41, TP42, TP43, TP44, TP45, TP47, TP48, TP49, TP50, TP51, TP52, TP53, TP54, TP55, TP56, TP57, TP63, TP64, TP65, TP66, TP67, TP68, TP72, TP74, TP75, TP77, TP78: TEST-POINT; 2MM-TEST-POINT
TP3, TP4, TP5, TP6, TP7, TP8, TP9, TP10, TP11, TP12, TP13, TP14, TP15, TP16, TP17, TP22, TP35, TP36, TP37, TP38, TP40, TP102, TP109, TP110, TP121, TP129, TP130, TP132, TP133, TP136, TP138, TP139, TP140, TP141, TP144, TP154, TP156, TP160, TP161, TP163, TP164, TP165, TP166, TP167, TP168: TEST-POINT3X4; PAD.03X.04
U1: RCLAMP0504FB; SC70-6
U2: DS90CR218AMTD/NOPB; MTD48_TEX-L
U3: SFEM016GB1EA1TO-I-GE-121-STD; BGA-153(11.5X13)(EMMC-BA)
U4: SN74AUC1G07DCKR; SOT-353_SC-70-5
U5: TS5A21366; VSSOP-8_2.3x2mm_P0.5mm
U7: OSD3358-1G-ISM; U-Octavo-OSD335X-BGA-256
U10: TLVH431; SOT-23
U11: TCAN330; SOT-23-8
U12, U13: MIC842LYC5; SOT-353_SC-70-5
U14: MAX4211FETE; QFN-16-1EP_4x4mm_P0.65mm_EP2.1x2.1mm
U15: TPS62112; Texas_RSA_VQFN-16-1EP_4x4mm_P0.65mm_EP2.7x2.7mm
U16: MAX7310ATE+; QFN-16-1EP_4x4mm_P0.65mm_EP2.1x2.1mm
Y1: ECS-240-12-30BQ-AEN-TR; CRYSTAL-5X3.2-4SMD
Y2: ABS07-32.768KHZ-T; CRYSTAL_3.2X1.5

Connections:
1.8V-A: C50.1, R21.2, U7.A7 (SYS_ADC_1P8V), U7.B7 (VREFP)
3.3V: C1.1, C2.1, C3.1, C5.1, C6.1, C7.1, C8.1, C9.1, C11.1, C16.1, C17.1, C20.1, C21.1, C23.1, C24.1, C25.1, C26.1, C27.1, C28.1, C31.2, C42.1, C43.1, C45.1, C46.1, C47.1, C48.1, C49.1, J6.4 (VDD), JP1.1, R1.1, R20.2, R22.2, R25.1, RA1.5 (55), RA1.10 (55), RA2.5 (55), RA2.10 (55), RA3.5 (55), RA3.10 (55), RA5.5, RA5.6, RA5.7, RA5.8, TP2.1, U2.12 (LVDS_VCC), U2.20 (PLL_VCC), U2.28 (VCC_2), U2.36 (VCC_3), U2.42 (VCC_4), U2.48 (VCC), U3.C6 (VDDQ), U3.E6 (VDDIO), U3.F5 (VDDIO), U3.J10 (VDDIO), U3.K9 (VDDIO), U3.M4 (VDDQ), U3.N4 (VDDQ), U3.P3 (VDDQ), U3.P5 (VDDQ), U7.F6 (SYS_VDD1_3P3V@1), U7.F7 (SYS_VDD1_3P3V@2), U7.G6 (SYS_VDD1_3P3V@3), U7.G7 (SYS_VDD1_3P3V@4), U11.3 (VCC)
3.3VA: Q1.2 (E), R23.2, R28.2, TP165.P$1 (1), U7.F8 (SYS_VDD3_3P3V@1), U7.F9 (VDDSHV4), U7.G8 (SYS_VDD3_3P3V@2), U7.G9 (VDDSHV5), U7.H7 (SYS_VDD3_3P3V@3), U7.H8 (SYS_VDD3_3P3V@4), U7.H9 (VDDSHV6), U7.J7 (SYS_VDD3_3P3V@5), U7.J8 (SYS_VDD3_3P3V@6), U7.J9 (VDDSHV1), U7.K8 (SYS_VDD3_3P3V@7), U7.K9 (VDDSHV2), U7.L8 (SYS_VDD3_3P3V@8), U7.L9 (VDDSHV3)
5V: C14.1, C36.1, L1.2, R62.2, TP49.1, U7.P10 (VIN_AC@1), U7.R10 (VIN_AC@2), U7.T10 (VIN_AC@3), U15.10 (FB)
/OSD3358: SIP A (PWR)/EEPROM_WP: J5.3, U7.M2 (EEPROM_WP)
/OSD3358: SIP A (PWR)/I2C0_SCL: J5.1, U7.C10 (I2C0_SCL), U7.D10 (PMIC_SCL)
/OSD3358: SIP A (PWR)/I2C0_SDA: J5.2, U7.C11 (I2C0_SDA), U7.D11 (PMIC_SDA)
/OSD3358: SIP A (PWR)/PMIC_PGOOD: TP110.P$1 (1), U4.2 (A), U7.N12 (PMIC_PGOOD), U7.P11 (PWRONRSTN)
/OSD3358: SIP B (USB, XTAL, ADC)/OSC0_GND: C19.1, C22.1, U7.N15 (OSC0_GND), Y1.2, Y1.4
/OSD3358: SIP B (USB, XTAL, ADC)/OSC0_IN: C19.2, R13.2, U7.P16 (OSC0_IN), Y1.1
/OSD3358: SIP B (USB, XTAL, ADC)/OSC0_OUT: C22.2, R13.1, U7.N16 (OSC0_OUT), Y1.3
/OSD3358: SIP C (SD, eMMC, PRU)/EMMC_CLK: RA2.9 (99), U3.M6 (SCK), U7.P2 (GPMC_CSN1)
/OSD3358: SIP C (SD, eMMC, PRU)/EMMC_CMD: RA2.2 (22), U3.M5 (CMD), U7.P1 (GPMC_CSN2)
/OSD3358: SIP C (SD, eMMC, PRU)/EMMC_D0: RA2.6 (66), U3.A3 (D0), U7.R3 (GPMC_AD0)
/OSD3358: SIP C (SD, eMMC, PRU)/EMMC_D1: RA3.1 (11), U3.A4 (D1), U7.R2 (GPMC_AD1)
/OSD3358: SIP C (SD, eMMC, PRU)/EMMC_D2: RA3.9 (99), U3.A5 (D2), U7.R1 (GPMC_AD2)
/OSD3358: SIP C (SD, eMMC, PRU)/EMMC_D3: RA2.4 (44), U3.B2 (D3), U7.T3 (GPMC_AD3)
/OSD3358: SIP C (SD, eMMC, PRU)/EMMC_D4: RA2.7 (77), U3.B3 (D4), U7.T2 (GPMC_AD4)
/OSD3358: SIP C (SD, eMMC, PRU)/EMMC_D5: RA2.8 (88), U3.B4 (D5), U7.T1 (GPMC_AD5)
/OSD3358: SIP C (SD, eMMC, PRU)/EMMC_D6: RA3.8 (88), U3.B5 (D6), U7.P4 (GPMC_AD6)
/OSD3358: SIP C (SD, eMMC, PRU)/EMMC_D7: RA3.2 (22), U3.B6 (D7), U7.R4 (GPMC_AD7)
/OSD3358: SIP C (SD, eMMC, PRU)/PRU_BUS.PRU0_0: TP30.1, U2.24 (RXOUT0), U7.A1 (MCASP0_ACLKX)
/OSD3358: SIP C (SD, eMMC, PRU)/PRU_BUS.PRU0_1: TP29.1, U2.26 (RXOUT1), U7.A2 (MCASP0_FSX)
/OSD3358: SIP C (SD, eMMC, PRU)/PRU_BUS.PRU0_2: TP28.1, U2.27 (RXOUT2), U7.B2 (MCASP0_AXR0)
/OSD3358: SIP C (SD, eMMC, PRU)/PRU_BUS.PRU0_3: TP27.1, U2.29 (RXOUT3), U7.B1 (MCASP0_AHCLKR)
/OSD3358: SIP C (SD, eMMC, PRU)/PRU_BUS.PRU0_4: TP26.1, U2.30 (RXOUT4), U7.A3 (MCASP0_ACLKR)
/OSD3358: SIP C (SD, eMMC, PRU)/PRU_BUS.PRU0_5: TP24.1, U2.31 (RXOUT5), U7.B3 (MCASP0_FSR)
/OSD3358: SIP C (SD, eMMC, PRU)/PRU_BUS.PRU0_6: TP23.1, U2.33 (RXOUT6), U7.C3 (MCASP0_AXR1)
/OSD3358: SIP C (SD, eMMC, PRU)/PRU_BUS.PRU0_7: R11.2, TP21.1, U7.C4 (MCASP0_AHCLKX)
/OSD3358: SIP C (SD, eMMC, PRU)/PRU_BUS.PRU_16_CLK: TP20.1, U2.23 (RXCLKOUT), U7.B4 (XDMA_EVENT_INTR1)
/OSD3358: SIP C (SD, eMMC, PRU)/~EMMC_RST: RA2.3 (33), U3.K5 (~RST), U7.R13 (GPMC_A4)
/OSD3358: SIP D (BOOT)/SYSBOOT0: RA5.14, U7.G3 (LCD_DATA0)
/OSD3358: SIP D (BOOT)/SYSBOOT1: RA5.13, U7.G2 (LCD_DATA1)
/OSD3358: SIP D (BOOT)/SYSBOOT3: RA5.11, U7.H3 (LCD_DATA3)
/OSD3358: SIP D (BOOT)/SYSBOOT4: RA5.10, U7.H2 (LCD_DATA4)
/OSD3358: SIP D (BOOT)/SYSBOOT5: RA5.15, U7.H1 (LCD_DATA5)
/OSD3358: SIP D (BOOT)/SYSBOOT6: RA5.16, U7.J3 (LCD_DATA6)
/OSD3358: SIP D (BOOT)/SYSBOOT7: RA4.16, U7.J2 (LCD_DATA7)
/OSD3358: SIP D (BOOT)/SYSBOOT8: RA4.15, U7.J1 (LCD_DATA8)
/OSD3358: SIP D (BOOT)/SYSBOOT9: RA4.14, U7.K3 (LCD_DATA9)
/OSD3358: SIP D (BOOT)/SYSBOOT10: RA4.13, U7.K2 (LCD_DATA10)
/OSD3358: SIP D (BOOT)/SYSBOOT11: RA4.12, U7.K1 (LCD_DATA11)
/OSD3358: SIP D (BOOT)/SYSBOOT12: RA4.11, U7.L3 (LCD_DATA12)
/OSD3358: SIP D (BOOT)/SYSBOOT13: RA4.10, U7.L2 (LCD_DATA13)
/OSD3358: SIP D (BOOT)/SYSBOOT14: RA5.9, U7.L1 (LCD_DATA14)
/OSD3358: SIP D (BOOT)/SYSBOOT15: RA4.9, U7.M3 (LCD_DATA15)
/Power (OPD)/AD0: R57.1, R58.2, R69.2, R70.1, U16.1 (AD0)
/Power (OPD)/AD1: R55.1, R56.2, R67.2, R68.1, U16.2 (AD1)
/Power (OPD)/AD2: R53.1, R54.2, R65.2, R66.1, U16.3 (AD2)
/Power (OPD)/CB-RESET: R39.2, TP54.1, U14.9 (CIN2-), U16.9 (IO4)
/Power (OPD)/CB_CTRL: Q2.1 (G), Q5.3 (G), R64.1, TP52.1, U14.3 (LE), U14.4 (COUT1), U14.6 (COUT2)
/Power (OPD)/ON/~OFF: C15.2, C34.1, Q4.1 (G), R46.2, R49.2, TP50.1, U5.8 (Vcc), U14.1 (VCC), U16.8 (IO3)
/Power (OPD)/PEN-SCL-FILT: Q3.6 (D), R37.2, R65.1, R67.1, R69.1, TP42.1, TP66.1, U16.15 (SCL)
/Power (OPD)/PEN-SDA-FILT: Q3.4 (D), R45.2, R66.2, R68.2, R70.2, TP41.1, TP65.1, U16.16 (SDA)
/Power (OPD)/~FAULT: Q2.3 (D), R32.1, TP45.1, U16.7 (IO2)
C3-UART-RX: J4.38, R18.2
C3-UART-TX: J4.37, R19.2
CAN2_H: J4.17, J4.18, U11.7 (CANH)
CAN2_L: J4.19, J4.20, U11.6 (CANL)
GND: C1.2, C2.2, C3.2, C4.2, C5.2, C6.2, C7.2, C8.2, C9.2, C10.2, C11.2, C12.2, C13.2, C14.2, C15.1, C16.2, C17.2, C18.2, C20.2, C21.2, C23.2, C24.2, C25.2, C26.2, C27.2, C28.2, C31.1, C32.2, C34.2, C35.2, C36.2, C37.2, C38.2, C39.1, C40.2, C41.2, C42.2, C43.2, C44.2, C45.2, C46.2, C47.2, C48.2, C49.2, C51.2, D1.1 (K), D2.1 (K), D3.1 (K), D4.1 (K), D5.1 (K), D6.1 (K), D7.1 (K), D8.1 (K), J1.3 (GND), J1.6 (GND), J1.9 (GND), J1.PAD1 (PAD), J1.PAD2 (PAD), J3.1, J4.27, J4.28, J4.29, J4.30, J5.4, J6.6 (VSS), J6.CGND1 (CGND), J6.CGND2 (CGND), J6.CGND3 (CGND), J6.CGND4 (CGND), J6.CGND5 (CGND), J6.CGND6 (CGND), J6.GND (VSS), Q2.2 (S), Q4.2 (S), R11.1, R12.1, R15.1, R24.1, R33.1, R39.1, R42.1, R46.1, R51.1, R54.1, R56.1, R58.1, RA4.1, RA4.2, RA4.3, RA4.4, RA4.5, RA4.6, RA4.7, RA4.8, RA5.1, RA5.2, RA5.3, RA5.4, TP72.1, TP74.1, TP75.1, TP77.1, TP78.1, U1.2 (GND), U2.3 (GND), U2.7 (GND), U2.13 (GND), U2.18 (GND), U2.19 (GND), U2.21 (GND), U2.25 (GND), U2.32 (GND), U2.38 (GND), U2.44 (GND), U3.A6 (VSSIO), U3.C4 (VSSQ), U3.E7 (VSSIO), U3.G5 (VSSIO), U3.H10 (VSSIO), U3.J5 (VSSIO), U3.K8 (VSSIO), U3.N2 (VSSQ), U3.N5 (VSSQ), U3.P4 (VSSQ), U3.P6 (VSSQ), U4.3 (GND), U5.4 (GND), U7.D8 (DGND@1), U7.D9 (DGND@2), U7.E5 (DGND@3), U7.E6 (DGND@4), U7.E7 (DGND@5), U7.E8 (DGND@6), U7.E9 (DGND@7), U7.E10 (DGND@8), U7.E11 (DGND@9), U7.E12 (DGND@10), U7.F5 (DGND@11), U7.F12 (DGND@12), U7.G5 (DGND@13), U7.G12 (DGND@14), U7.H4 (DGND@15), U7.H5 (DGND@16), U7.H12 (DGND@17), U7.H13 (DGND@18), U7.J4 (DGND@19), U7.J5 (DGND@20), U7.J12 (DGND@21), U7.J13 (DGND@22), U7.K5 (DGND@23), U7.K12 (DGND@24), U7.L5 (DGND@25), U7.L12 (DGND@26), U7.L14 (USB1_ID), U7.M5 (DGND@27), U7.M6 (DGND@28), U7.M7 (DGND@29), U7.M8 (DGND@30), U7.M9 (DGND@31), U7.M10 (DGND@32), U7.M11 (DGND@33), U7.M12 (DGND@34), U7.N8 (DGND@35), U7.N9 (DGND@36), U11.2 (GND), U12.2 (GND), U13.2 (GND), U14.7 (GND), U14.17 (GND), U15.1 (GND), U15.5 (SYNC), U15.6 (LBO), U15.7 (LBI), U15.9 (GND), U15.11 (GND), U15.12 (GND), U15.16 (GND), U15.17 (GND), U16.6 (GND), U16.17 (GND)
unnamed: C33.1, R33.2, R38.2
unnamed: D1.2 (A), R1.2
unnamed: D2.2 (A), R2.2
unnamed: D3.2 (A), R3.2
unnamed: D4.2 (A), R4.2
unnamed: D5.2 (A), R5.2
unnamed: D6.2 (A), R49.1
unnamed: D7.2 (A), R61.1
unnamed: D8.2 (A), R62.1
unnamed: J4.33, J4.34
unnamed: J4.35, J4.36
unnamed: J4.39, J4.40
unnamed: J6.CD (CD#), RA1.6 (66), TP22.P$1 (1), U7.C14 (SPI0_CS1)
unnamed: J6.5 (CLK), RA1.3 (33), U7.B15 (MMC0_CLK)
unnamed: J6.3 (CMD/DI), RA1.8 (88), U7.B16 (MMC0_CMD)
unnamed: J6.7 (DAT0/DO), RA1.7 (77), U7.A16 (MMC0_DAT0)
unnamed: J6.8 (DAT1), RA1.4 (44), U7.A15 (MMC0_DAT1)
unnamed: J6.1 (DAT2), RA1.9 (99), U7.C16 (MMC0_DAT2)
unnamed: J6.2 (DAT3/CS), RA1.2 (22), U7.C15 (MMC0_DAT3)
unnamed: L1.1, U15.14 (SW), U15.15 (SW)
unnamed: Q1.1 (B), R23.1, U10.2 (K)
unnamed: C18.1, Q1.3 (C), R31.1, TP164.P$1 (1), U4.5 (VCC), U7.K11 (SYS_RTC_1P8V@1), U7.L11 (SYS_RTC_1P8V@2), U10.3 (A)
unnamed: Q3.1 (G), R35.2
unnamed: Q3.5 (S), R48.2
unnamed: Q3.3 (G), R43.2
unnamed: Q3.2 (S), R41.2
unnamed: Q4.3 (D), Q6.3 (G), R52.1
unnamed: Q5.4 (S), R63.2, R64.2, U14.15 (RS-)
unnamed: TP4.P$1 (1), U7.B10 (UART1_CTSN)
unnamed: TP5.P$1 (1), U7.C1 (TDI)
unnamed: TP6.P$1 (1), U7.C2 (TDO)
unnamed: TP7.P$1 (1), U7.D1 (TCK)
unnamed: TP8.P$1 (1), U7.D2 (TMS)
unnamed: TP9.P$1 (1), U7.P6 (GPMC_AD12)
unnamed: TP10.P$1 (1), U7.R6 (GPMC_AD13)
unnamed: TP11.P$1 (1), U7.T6 (GPMC_AD14)
unnamed: TP12.P$1 (1), U7.M14 (USB1_DRVVBUS)
unnamed: TP13.P$1 (1), U7.A10 (UART1_RTSN)
unnamed: TP14.P$1 (1), U7.P7 (GPMC_AD15)
unnamed: TP15.P$1 (1), U7.L15 (USB1_DP)
unnamed: TP16.P$1 (1), U7.L16 (USB1_DM)
unnamed: TP17.P$1 (1), U7.M15 (USB1_VBUS)
unnamed: TP35.P$1 (1), U11.5 (SHDN)
unnamed: TP36.P$1 (1), U7.B8 (AIN1)
unnamed: TP37.P$1 (1), U7.B6 (AIN2)
unnamed: TP38.P$1 (1), U7.C6 (AIN3)
unnamed: TP40.P$1 (1), U11.8 (S)
unnamed: TP102.P$1 (1), U7.T11 (PMIC_PB_IN)
unnamed: TP121.P$1 (1), U7.N10 (PMIC_POWER_EN), U7.N11 (PMIC_PWR_EN)
unnamed: TP129.P$1 (1), U7.N6 (PMIC_TS)
unnamed: TP130.P$1 (1), U7.N7 (PMIC_BAT_SENSE), U7.P8 (VIN_BAT@1), U7.R8 (VIN_BAT@2), U7.T8 (VIN_BAT@3)
unnamed: TP132.P$1 (1), U7.N4 (PMIC_LDO_PGOOD), U7.N5 (RTC_PWRONRSTN)
unnamed: TP133.P$1 (1), U7.N13 (PMIC_MUX_IN)
unnamed: TP136.P$1 (1), U7.M13 (PMIC_NRESET)
unnamed: TP138.P$1 (1), U7.K14 (USB0_ID)
unnamed: TP139.P$1 (1), U7.J15 (USB0_DRVVBUS)
unnamed: TP140.P$1 (1), U7.L4 (PMIC_NWAKEUP), U7.M4 (EXT_WAKEUP)
unnamed: TP141.P$1 (1), U7.K13 (USB0_CE)
unnamed: TP144.P$1 (1), U7.L13 (USB1_CE)
unnamed: TP154.P$1 (1), U7.G4 (VDD_CORE)
unnamed: TP156.P$1 (1), U7.F4 (VDDS_DDR)
unnamed: TP160.P$1 (1), U7.F13 (VDD_MPU)
unnamed: TP161.P$1 (1), U7.F11 (SYS_VDD2_3P3V@1), U7.G11 (SYS_VDD2_3P3V@2)
unnamed: TP163.P$1 (1), U7.F10 (SYS_VDD_1P8V@1), U7.G10 (SYS_VDD_1P8V@2), U7.H10 (SYS_VDD_1P8V@3), U7.H11 (SYS_VDD_1P8V@4), U7.J10 (SYS_VDD_1P8V@5), U7.J11 (SYS_VDD_1P8V@6), U7.K10 (SYS_VDD_1P8V@7), U7.L10 (SYS_VDD_1P8V@8)
unnamed: TP166.P$1 (1), U7.G13 (VDDS_PLL)
unnamed: TP167.P$1 (1), U7.D4 (EXTINTN), U7.E4 (PMIC_NINT)
unnamed: TP168.P$1 (1), U7.D6 (PMIC_MUX_OUT)
unnamed: R30.1, U2.11 (RXIN1+)
unnamed: R30.2, U2.10 (RXIN1-)
unnamed: R29.1, U2.15 (RXIN2+)
unnamed: R29.2, U2.14 (RXIN2-)
unnamed: JP1.2, U2.22 (~PWR_DWN)
unnamed: C10.1, C12.1, U3.C2 (VDDI)
unnamed: R18.1, U5.2 (COM1)
unnamed: R19.1, U5.6 (COM2)
unnamed: R15.2, U7.M16 (RTC_KALDO_ENN)
unnamed: C50.2, U7.A9 (AGND_ADC), U7.B9 (VREFN)
unnamed: R22.1, U7.E2 (EMU0)
unnamed: R20.1, U7.E3 (EMU1)
unnamed: C29.2, C30.2, U7.B5 (OSC1_GND)
unnamed: C30.1, R27.2, U7.A6 (OSC1_IN), Y2.2
unnamed: C29.1, R27.1, U7.A5 (OSC1_OUT), Y2.1
unnamed: R24.2, U7.D3 (TRSTN)
unnamed: R2.1, U7.P13 (GPMC_A5)
unnamed: R3.1, U7.T14 (GPMC_A6)
unnamed: R4.1, U7.R14 (GPMC_A7)
unnamed: R5.1, U7.P14 (GPMC_A8)
unnamed: R28.1, R31.2, U10.1 (REF)
unnamed: U7.B11 (UART1_TXD), U11.4 (RXD)
unnamed: U7.A11 (UART1_RXD), U11.1 (TXD)
unnamed: C32.1, R36.1, R37.1, U12.1 (INP)
unnamed: R35.1, TP44.1, U12.4 (OUT)
unnamed: C35.1, R44.1, R45.1, U13.1 (INP)
unnamed: R43.1, TP43.1, U13.4 (OUT)
unnamed: R50.1, R51.2, TP57.1, U14.10 (CIN1+)
unnamed: R42.2, R47.1, TP47.1, U14.11 (CIN1-)
unnamed: R47.2, U14.8 (CIN2+), U14.12 (REF)
unnamed: R38.1, U14.5 (INHIBIT)
unnamed: R50.2, U14.14 (IOUT)
unnamed: TP64.1, U14.13 (POUT)
unnamed: C44.1, Q6.1 (D), Q6.2 (D), Q6.5 (D), Q6.6 (D), R63.1, U14.16 (RS+)
unnamed: TP48.1, U15.13 (PG)
unnamed: TP67.1, U16.4 (IO0)
unnamed: TP68.1, U16.5 (IO1)
unnamed: R26.2, TP51.1, U16.10 (IO5)
unnamed: TP53.1, U16.11 (IO6)
unnamed: R12.2, TP56.1, U5.3 (IN2), U5.7 (IN1), U16.12 (IO7)
unnamed: R72.1, U16.13 (~RESET)
OPD_PWR: J4.15, J4.16, R71.1
OPD_SCL: J4.13, J4.14, R48.1
OPD_SDA: J4.11, J4.12, R41.1
OUT1_N: J2.5, J2.6, R6.2, U2.8 (RXIN0-)
OUT1_P: J2.7, J2.8, R6.1, U2.9 (RXIN0+)
SENSOR_ENABLE: J2.13, J2.14, U7.F3 (LCD_VSYNC)
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

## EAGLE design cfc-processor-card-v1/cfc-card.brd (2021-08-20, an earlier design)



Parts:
C4: 0.1uF; .0603-A
J1: ORESAT-DEBUG-CONNECTOR-ALL; TE_2-1734592-0
J2: J-SAMTEC-TFM-110-X1-XXX-D-RA; MPN TFM-110-01-L-D-RA
J4: TFM-120-01-L-D-RA; J-SAMTEC-TFM-120-X1-XXX-D-RA
PCB1: ORESAT-CARD-V1.3-GENERIC-0RF
TP183, TP184: TEST-POINT3X4; PAD.03X.04
U1: RCLAMP0504FB; SC70-6
U$1: FLIGHMARKERNEW; FLIGHTMARKER_NEW_BOARDS

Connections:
!SD: J4.39, J4.40
CAN1_H: J4.33, J4.34, TP184.P$1
CAN1_L: J4.35, J4.36, TP183.P$1
CAN2_H: J4.17, J4.18; also elsewhere on the board
CAN2_L: J4.19, J4.20; also elsewhere on the board
EEPROM_WP: J1.20 (DEBUG-3); also elsewhere on the board
GND: C4.2, J1.3 (GND), J1.6 (GND), J1.9 (GND), J1.PAD1 (PAD), J1.PAD2 (PAD), J4.27, J4.28, J4.29, J4.30, J4.31, J4.32, J4.37, J4.38, U1.2 (GND); also elsewhere on the board
I2C0_SCL: J1.18 (DEBUG-1), U1.6 (I4); also elsewhere on the board
I2C0_SDA: J1.19 (DEBUG-2), U1.4 (I3); also elsewhere on the board
unnamed: J4.1, J4.2
OPD_PWR: J4.15, J4.16; also elsewhere on the board
OPD_SCL: J4.13, J4.14; also elsewhere on the board
OPD_SDA: J4.11, J4.12; also elsewhere on the board
OUT1_N: J2.5, J2.6; also elsewhere on the board
OUT1_P: J2.7, J2.8; also elsewhere on the board
SENSOR_ENABLE: J2.13, J2.14; also elsewhere on the board
SPARE1: J4.9, J4.10
SPARE2: J4.7, J4.8
SPARE3: J4.5, J4.6
SPARE4: J4.3, J4.4
SPI1_CLK: J2.17, J2.18; also elsewhere on the board
SPI1_MISO: J2.15, J2.16; also elsewhere on the board
SPI1_MOSI: J2.19, J2.20; also elsewhere on the board
TEC_ENABLE: J2.9, J2.10; also elsewhere on the board
THERM+: J2.11, J2.12; also elsewhere on the board
TXCLK_N: J2.1, J2.2; also elsewhere on the board
TXCLK_P: J2.3, J2.4; also elsewhere on the board
UART0_RX: J1.12 (CARD-RX); also elsewhere on the board
UART0_TX: J1.13 (CARD-TX); also elsewhere on the board
USB_CLI_N: J1.5 (DEVICE-D-), U1.3 (I2); also elsewhere on the board
USB_CLI_P: J1.4 (DEVICE-D+), U1.1 (I1); also elsewhere on the board
USB_CLI_VBUS: J1.1 (VBUSP), J1.2 (VBUSP); also elsewhere on the board
VBUS: J4.21, J4.22, J4.23, J4.24, J4.25, J4.26; also elsewhere on the board
VDD: C4.1, U1.5 (VCC); also elsewhere on the board
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

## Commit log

2020-07-16 first go around on the channel link test board
    [channel-link-test-board.brd, channel-link-test-board.sch]
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2020-07-19 moved LVDS lines so I could bypass the LVDS VCC
    [channel-link-test-board.brd, channel-link-test-board.sch]
2020-07-20 ocd fixes
    [channel-link-test-board.brd, channel-link-test-board.sch]
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2021-01-21 Mods from Oliver and Scott; more testpoints, stitching, ground points.
    [PIRT1280A1-12-breakout.brd, PIRT1280A1-12-breakout.sch]
2021-01-26 Prototype of PIRT sensor and an example LT3042 power supply layout for one of the supplies.
    [PIRT1280A1-12-breakout.brd, PIRT1280A1-12-breakout.sch]
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2021-05-10 added PIRT1280 BOM, used internal library in carrier, added attributes
    [PIRT1280 Carrier BOM.xlsx, PIRT1280A1-12-carrier.brd, PIRT1280A1-12-carrier.sch]
2021-05-10 Fixed BOM (a lot of wrong packages, no mfr, no descriptions, wrong formatting). Fixed 16 MHz crystal attributes.
    [PIRT1280 Carrier BOM.xlsx, PIRT1280A1-12-carrier.brd, PIRT1280A1-12-carrier.sch]
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2021-07-22 Fix up ERC warnings
    [cfc_emulator.kicad_sch]
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2021-08-02 fixed resistor array value
    [cfc-card.brd, cfc-card.sch]
2021-08-18 Fixed R27 attributes, and fixed names layer
    [cfc-sensor-card.brd, cfc-sensor-card.sch]
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2021-08-20 Updated OPD address resistors, LED resistors (AAAAAUGH MY EYES), and OPD shunt resistor to give the CFC sensor card addrss 0x1E and a 2.95 A current limit.
    [cfc-sensor-card-bom.xlsx, cfc-sensor-card.brd, cfc-sensor-card.sch]
2022-11-08 Revamp the CFC hardware repo to keep v1 (giant copper block version) and start v2 (radiator version).
    [CFCcard.DXF, CFCdxf.DXF, cfc-sensor-card-bom.xlsx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]
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2022-11-08 New KiCAD project, schematic, and PCB layout for v2 of the CFC Sensor Board. Note that the schematic is empty, but the board reflects the 2022-09-15 sensor card outline from OnShape.
    [cfc-sensor-card.kicad_pcb, cfc-sensor-card.kicad_sch]
2022-11-08 Adding PIRT sensor. Needs a double check, and the rest of the symbol.
    [cfc-sensor-card.kicad_pcb, cfc-sensor-card.kicad_sch]
2022-11-09 Make sensor card thermal strap fastener passthroughts 5 mm so we can use a 4.5 mm washer.
    [cfc-sensor-card.kicad_pcb]
2022-11-22 Add new DXF with bottom layer keepouts from the lens mount, and add it to the user.documentation layer.
    [cfc-sensor-card.kicad_pcb]
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2023-01-25 Changes from board fab: fixed card outline center hole (no fill), excluded some new violations, changed minimum mask web to 0.
    [cfc-sensor-card.kicad_pcb]
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2023-02-20 OPD CB shunt resistor is 10m, not 100m. Cleanup documentation. Also clean up documentation on other pages.
    [cfc-sensor-card.kicad_sch, connectors.kicad_sch, opd.kicad_sch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]
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2023-05-13 Added note to Ben about a Ben Idea.
    [cfc-minibackplane.dxf]
2023-05-14 Created a first revision of the mini backplane
    [cfc-minibackplane.kicad_pcb, cfc-minibackplane.kicad_sch]
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2023-05-14 Fixed silkscreen
    [cfc-minibackplane.kicad_pcb]
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2023-06-01 Added formatted BOM for the minibackplane, including board connectors.
    [cfc-minibackplane-bom.xlsx]
2023-06-19 Added not on Trinket wiring bug.
    [cfc-minibackplane.kicad_sch]
2023-07-16 Fixed wrong NPs in CFC sensor card OPD. Updated to KiCAD 7.
    [cfc-sensor-card.kicad_pcb, cfc-sensor-card.kicad_sch, connectors.kicad_sch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]
2023-08-04 Added soft start to sensor card and cleaned up some KiCad warnings
    [cfc-sensor-card.kicad_pcb, opd.kicad_sch, pirt.kicad_sch]
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2025-06-12 Initial conversion of cfc processor board from Eagle to KiCAD 9
    Still using converted Eagle symbols and footprints.
    [cfc-card.kicad_sch, connectors.kicad_sch, opd.kicad_sch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]
2025-08-28 Clean up CFC Processor Card from Scott's initial import which was Gerber identical to origianl EAGLE schematic. Interestingly, this version was already changed for the v2 backplane which is great. Al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
    [cfc-card.kicad_pcb, cfc-card.kicad_sch, cfc-processor-sch-boot.kicad_sch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]
2025-08-30 Big cleanup - fixed a billion ERCs and DRCs. Switched a bunch of parts over to OreSat parts. Added analog switch on UART so CFC processor can talk serial to C3. Last thing left: clean up passives wit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
    [cfc-card.kicad_pcb, cfc-processor-sch-boot.kicad_sch, connectors.kicad_sch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]
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2025-09-13 Big sweep through to clean up from v2.0 to v2.1 board. Cleaned up all of the Github issues, and even added a MPS2410A CC driver to run the TEC for increased efficiency. Left old switch on board just 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
    [cfc-sensor-card-sch-tec.kicad_sch, cfc-sensor-card.kicad_pcb, cfc-sensor-card.kicad_sch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]
2025-09-13 renamed files to standard filenames, removed html file.
    [cfc-sensor-card-sch-connectors.kicad_sch, cfc-sensor-card-sch-opd.kicad_sch, cfc-sensor-card-sch-pirt.kicad_sch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]
2025-09-14 Final polish on schematic and PCB. Cleaned up BOM, fixed github issues which were not really issues. Lots of BOM cleanup, with MPNs and DPNs.
    [cfc-card.kicad_pcb, cfc-card.kicad_sch, cfc-processor-sch-boot.kicad_sch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]
2025-09-14 Fix and complete BOM, fix lots of little layout issue and footprint inconsistancies, and polish. Ready to go!
    [cfc-sensor-card-sch-connectors.kicad_sch, cfc-sensor-card-sch-opd.kicad_sch, cfc-sensor-card-sch-pirt.kicad_sch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]
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2025-09-15 Rename old processor board since it's old and don't want people going there. Eventually, we'll remove, but those cards are still in use so worth it to have both for right now.
    [cfc-card.brd, cfc-card.sch]
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2025-09-15 Fixed up crappy symbol on OPD; no change to layout, just schematic and link to PCB.
    [cfc-processor-sch-power.kicad_sch, cfc-processor.kicad_pcb, cfc-processor.kicad_sch]
2026-06-23 Schematic Changes
    Made schematic into hierarchy view. Revised OPD to match modern OPD. Removed connectors page. Separated power sequencing and PIRT sensor into 2 pages.
    [cfc-sensor-card-sch-connectors.kicad_sch, cfc-sensor-card-sch-opd.kicad_sch, cfc-sensor-card-sch-pirt.kicad_sch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]
2026-06-24 CFC processor schematic Change
    changed to hierarchy view, changed all global net labels to hierarchy labels, changed all resistor, capacitor, and ground symbols to modern oresat labels. Deleted connectors sheet and added .history 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
    [cfc-processor-sch-Deserializer.kicad_sch, cfc-processor-sch-connectors.kicad_sch, cfc-processor-sch-power.kicad_sch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]
2026-06-24 Updated OPD
    couple of resistors and caps added to schematic. Changed USB ESD clamp VDD to 3.3v instead of octavo created VDD line.
    [cfc-processor-sch-Deserializer.kicad_sch, cfc-processor-sch-power.kicad_sch, cfc-processor-sch-sip-a.kicad_sch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]
2026-06-25 Update
    Added pull down resistors and removed therm + and sensor enable and added i2c support for cfc sensor card.
    [cfc-processor-sch-power.kicad_sch, cfc-processor-sch-sip-a.kicad_sch, cfc-processor-sch-sip-b.kicad_sch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]
2026-06-27 Update
    Fixed a couple of library issues on testpoints and other misc components. Added Pull up resistors to 8 channel i2c ic
    [cfc-processor-sch-Deserializer.kicad_sch, cfc-processor-sch-power.kicad_sch, cfc-processor-sch-sip-a.kicad_sch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]
2026-06-28 Update
    Changed passive component footprints to 0603 no silk c. Fixed OPD UART termination resistor on cfc processor card. Added low temp co and tolerance resistor for NTC thermistor tec voltage divider.
    [cfc-processor-sch-power.kicad_sch, cfc-processor-sch-sip-b.kicad_sch, cfc-sensor-card-sch-opd.kicad_sch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]
2026-06-28 Update
    Cleaned up library preferences, added voltage controlled constant current note. Added RC filter to therm+ measurement made against the 2.5vref.
    [cfc-sensor-card-sch-tec.kicad_sch]
2026-06-30 Update
    Added bidirectional TEC control with DRV8212 IC. Added Sensor enable pin back to processor; in case of i2c hang up octavo can still disable sensor.
    [cfc-processor.kicad_sch, cfc-sensor-card-sch-tec.kicad_sch, cfc-sensor-card.kicad_sch]
2026-06-30 update
    Changed a couple of test points on OPD to through hole test points. Added tables to DRV8212 on sensor schematic+ other visual improvements to processor schematic.
    [cfc-processor-sch-power.kicad_sch, cfc-processor-sch-sip-b.kicad_sch, cfc-processor-sch-sip-c.kicad_sch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]

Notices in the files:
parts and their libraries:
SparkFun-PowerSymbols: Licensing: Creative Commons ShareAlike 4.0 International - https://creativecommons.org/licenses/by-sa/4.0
